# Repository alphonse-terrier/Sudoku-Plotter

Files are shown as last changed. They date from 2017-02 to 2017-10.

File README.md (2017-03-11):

# Sudoku-Plotter

Tous les fichiers permettant la réalisation d' un bras mécanique travaillant en coordonnées polaires, permettant d’écrire un sudoku ou d’en résoudre un et à terme d’écrire tout type d’information.

Au niveau informatique, le bras doit identifier une grille de sudoku tracée sur une feuille, résoudre cette dernière par différentes méthodes de résolution. Ces méthodes doivent permettre éventuellement de créer des grilles de sudoku à compléter. Une fois le sudoku résolu, le stylo présent sur le bras doit pouvoir se déplacer pour écrire la solution de celui-ci (ou écrire un sudoku que l’utilisateur devra lui-même compléter). Le bras doit pouvoir également recopier tout type de document en noir et blanc.

La structure du bras sera réalisée en Makerbeam, tiges en métal se rapprochant dans leur utilisation des meccanos. Le pivotement du bras sera assuré par un moteur pas-à-pas dont le pignon sera en liaison appui-plan avec un roue dentée fixe. Ainsi la mise en mouvement du moteur entrainera sa rotation - et celle de toute la structure - autour de cette roue. Le stylo sera fixé sur une structure qui pourra se déplacer le long de deux tiges en métal. Cette structure sera mise en mouvement par un deuxième moteur pas-à-pas qui entrainera une courroie fixée à ses extrémités à celle-ci. Le stylo pourra être mis en contact avec la feuille grâce à un servomoteur.

La résolution d'un sudoku peut se faire par l'éxécution du fichier main.py dans un interpréteur Python 3.

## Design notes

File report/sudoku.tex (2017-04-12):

\title{Bras mécanique et sudoku}
\author{Laurent Tainturier \& Alphonse TERRIER}
\date{2016-2017}
\documentclass[12pt,a4paper]{report}
\usepackage[utf8]{inputenc}
\usepackage[T1]{fontenc}
\usepackage[french]{babel}
\usepackage{hyperref}
\usepackage{lmodern}
\usepackage{graphicx}
\usepackage{multirow}
\usepackage{listings}
\usepackage{enumitem}
\usepackage{stmaryrd}
\usepackage{animate}
\usepackage{url}
\usepackage{array}
\usepackage{amsmath, amsfonts, amssymb}
%\usepackage{minted}
\usepackage{color}
\usepackage{tabularx}
\usepackage{float}
\usepackage{caption}
\usepackage[backend=biber, autolang=other, sorting=none, style=science]{biblatex}
\usepackage[left=4cm,right=3cm,top=2.5cm,bottom=2.5cm]{geometry}
\usepackage{fancyvrb}
\frenchbsetup{StandardLists=true}
\newtheorem{theo}{Définition}[section]
\definecolor{lightgray}{gray}{.6}
\usepackage[dvipsnames]{xcolor}
\definecolor{yellow}{RGB}{225,220,0}
\hypersetup{pdfborder={0 0 0}}

\newenvironment{changemargin}[2]{\begin{list}{}{%
\setlength{\topsep}{0pt}%
\setlength{\leftmargin}{0pt}%
\setlength{\rightmargin}{0pt}%
\setlength{\listparindent}{\parindent}%
\setlength{\itemindent}{\parindent}%
\setlength{\parsep}{0pt plus 1pt}%
\addtolength{\leftmargin}{#1}%
\addtolength{\rightmargin}{#2}%
}\item }{\end{list}}

\usepackage{placeins}

%\addbibresource{bibli.bib}

\begin{document}
\FloatBarrier

\begin{titlepage}
\begin{changemargin}{-1cm}{0cm}
	\centering
	\vspace{5cm}
	{\scshape\huge Institut Supérieur d'Électronique de Paris \par}
	\vspace{1cm}
	{\scshape\LARGE TIPE\par}
	\vspace{1.5cm}
	{\fontsize{45}{45}\selectfont\bfseries Bras mécanique et sudoku\par}
	\vspace{2cm}
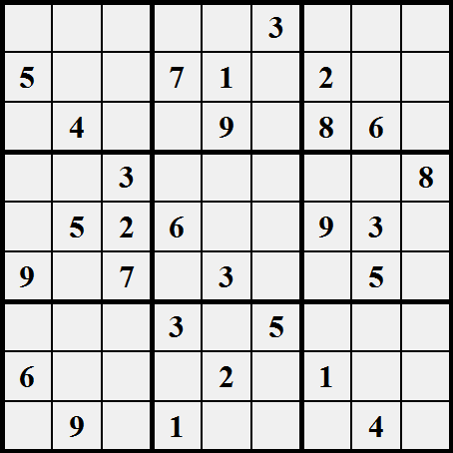
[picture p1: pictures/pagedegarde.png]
	\par\vspace{1.5cm}
	{\LARGE Laurent Tainturier \& Alphonse Terrier\par}
	\vfill
	\large supervisé par\par
	\large \bfseries M. Patrick COUVEZ

	\vfill

	{\large 2016-2017}
\end{changemargin}
\end{titlepage}

\tableofcontents
\addcontentsline{toc}{chapter}{Introduction}
	\chapter*{Introduction}
\footnote{Sauf mention contraire, les images et figures ont été réalisées par nos soins.}
	
	\chapter{Présentation et faits sur le sudoku}
	
	Le sudoku est un jeu sous forme de grille inspiré du carré latin et défini en 1979 par Howard Garns.
	
	Cette grille est carrée et est divisée en $n^2$ régions de $n^2$ cases. Elle possède ainsi $n^2$ colonnes, $n^2$ lignes et $n^4$ cases. Dans la version la plus commune : $n=3$. On appelle section, une ligne, une colonne ou une région

Une grille de sudoku est préremplie, le but du jeu étant de la compléter selon la règle suivante :
\begin{itemize}[label=--]
\item Chaque section doit contenir au moins une fois tous les de $1$ à $n^2$.
\end{itemize} 

Une grille est considérée comme sudoku seulement si sa solution est unique.

Le minimum de cases remplies au préalable pour espérer que la dite solution soit bien unique est de 17, cela a été prouvé par une équipe islandais en 2012.

	\chapter{Mécanique}	
	\section{Choix concernant la structure du bras}
	La premier défi qui s'est imposé à nous a été le choix d'une structure adéquate : solide et pratique. Notre choix s'est alors porté sur les Makerbeam. MakerBeam est un système de construction Open-Source basé sur des profilés ALU en T.
	
	L'écriture se fera en coordonnées polaires et non pas en coordonnées cartésiennes pour les raisons suivantes :
	\begin{itemize}[label=--]
	\item un système en coordonnées cartésiennes aurait été trop encombrant et un moins "portable" (dans un contexte notamment d'optimalité, comme exigé par le programme)
	\item c'est un défi technique de fabriquer un bras de ce type en coordonnées polaires
	\end{itemize}
	
Ainsi, un moteur pas-à-pas assurera la rotation $\theta$ du bras. Ce moteur s'auto-entrainera autour d'une roue dentée de 128 dents comme celle-ci et un roulement permettra la rotation de l'entièreté du bras :

\begin{figure}[!h]
 \center
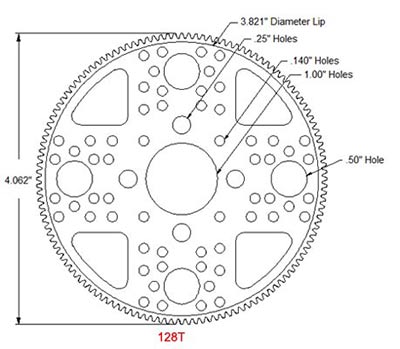
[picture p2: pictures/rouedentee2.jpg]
 
 \caption{Schéma de la roue dentée}
\end{figure}

De même la translation $r$ a été assurée par un deuxième moteur pas-à-pas et un système courroie/poulie. Cette translation s'est faite le long de deux axes de $272$ mm et de $8$ mm de diamètre.

	\section{Étude cinématique du mécanisme}
	La pièce 0 correspondra par la suite au bâti. La base du bras et le bâti seront supposés en liaison encastrement, alors qu'ils sont en réalité en liaison appui-plan, cependant les forces de frottements entre ces deux pièces sont telles quelles sont presque immobiles l'une par rapport à l'autre. La pièce 1 correspond à la structure du bras, reposant sur la roue dentée. La pièce 2 symbolise le chariot et la pièce 3 le stylo.

\begin{figure}[!h]
 \center
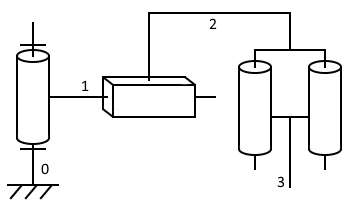
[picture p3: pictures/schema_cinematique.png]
 
 \caption{Schéma cinématique du mécanisme choisi}
\end{figure}

\begin{figure}[!h]
 \center
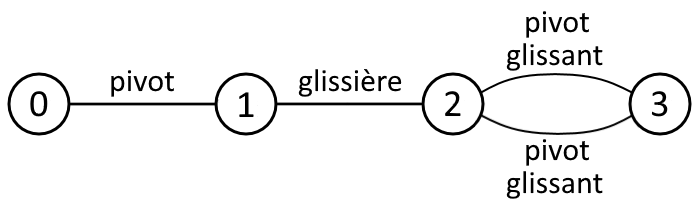
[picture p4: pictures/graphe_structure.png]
 
 \caption{Graphe de structure du mécanisme choisi}
\end{figure}

	Les deux liaisons en parallèle entre 2 et 3 peuvent être remplacés par une liaison équivalent ede torseur $\{ T_c (2/3) \}$ devant vérifier l'équation suivante: : 
	\begin{align*}
\{ T_c (2/3) \}_{B} = \{ T'_c (2/3) \}_{B} = \{ T''_c (2/3) \}_{B}
\end{align*}
On notera les liaisons entre les pièces 2 et 3 $L'_{2/3}$ et $L''_{2/3}$. On a alors:
\begin{align*}
\{ T'_c (2/3) \} =
\begin{array}{c}
	\\ \\ \\ 
\end{array} _{\forall P \in (B,\overrightarrow{z})}
\left\{
\begin{array}{cc}
	0 & 0 \\
	0 & 0 \\
	\gamma'_{2/3} & w'_{2/3} \\
\end{array}
\right\} _{x,y,z)}
\end{align*} 
\begin{align*}
\{ T''_c (2/3) \} = 
\begin{array}{c}
	\\ \\ \\ 
\end{array} _{\forall P \in (C, \overrightarrow{z})}
\left\{
\begin{array}{cc}
	0 & 0 \\
	0 & 0 \\
	\gamma''_{2/3} & w''_{2/3} \\
\end{array}
\right\} _{(x, y, z)}
\end{align*}
\begin{align*}
\mbox{Or } \overrightarrow{V}(B \in 2/3) 
&= \overrightarrow{V}(C \in 2/3)+\overrightarrow{\Omega}(2/3) \wedge \overrightarrow{CB}\\ 
&= w''_{2/3} \overrightarrow{z} + \gamma''_{2/3} \overrightarrow{z} \wedge BC \overrightarrow{x} \\
&= w''_{2/3} \overrightarrow{z} + \gamma''_{2/3}BC \overrightarrow{y}
\end{align*} 
\begin{align*}
\mbox{On a donc }
\{ T''_c (2/3) \} = 
\begin{array}{c}
	\\ \\ \\ 
\end{array} _{B}
\left\{
\begin{array}{cc}
	0 & 0 \\
	0 & \gamma''_{2/3}BC \\
	\gamma''_{2/3} & w''_{2/3} \\
\end{array}
\right\} _{(x, y, z)}
\end{align*}
\begin{align*}
\mbox{Donc }
\{ T_c (2/3) \} = 
\begin{array}{c}
	\\ \\ \\ 
\end{array} _B
\left\{
\begin{array}{cc}
	0 & 0 \\
	0 & 0 \\
	\gamma'_{2/3} & w'_{2/3} \\
\end{array}
\right\} _{x,y,z)} =
\begin{array}{c}
	\\ \\ \\ 
\end{array} _{B}
\left\{
\begin{array}{cc}
	0 & 0 \\
	0 & \gamma''_{2/3}BC \\
	\gamma''_{2/3} & w''_{2/3} \\
\end{array}
\right\} _{(x, y, z)}
\end{align*} 
\begin{align*}
\mbox{D'où le système d'équation : }
\left\{
\begin{array}{l}
0 = 0 \\
0 = 0 \\
\gamma'_{2/3} = \gamma''_{2/3} \\
0 = 0 \\
\gamma''_{2/3} = 0 \\
w'_{2/3} = w''_{2/3} \\
\end{array}
\right. 
\end{align*} 
\begin{align*}
\mbox{On en déduit } 
\{ T_c (2/3) \} = 
\begin{array}{c}
	\\ \\ \\ 
\end{array} _B
\left\{
\begin{array}{cc}
	0 & 0 \\
	0 & 0 \\
	0 & w'_{2/3} \\
\end{array}
\right\} _{x,y,z)}
\end{align*}

La liaison équivalente est donc une liaison glissière d'axe z, ce qui permet des déplacements verticaux du stylo, il peut ainsi être mis en contact avec la feuille.
On a alors le schéma de la figure \ref{Schema_cine_simp}.

\begin{figure}[!h]
 \center
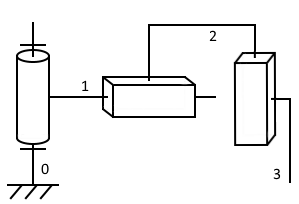
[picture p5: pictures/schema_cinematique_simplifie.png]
 
 \caption{Schéma cinématique équivalent au mécanisme choisi}
 \label{Schema_cine_simp}
\end{figure}

	\section{Difficultés rencontrées et solutions mises en place}
	Nous avons notamment rencontré des difficultés concernant le roulement utilisé. En effet, nous avions au préalable utilisé un roulement à billes comme celui-ci :
	
	\begin{figure}[!h]
 \center
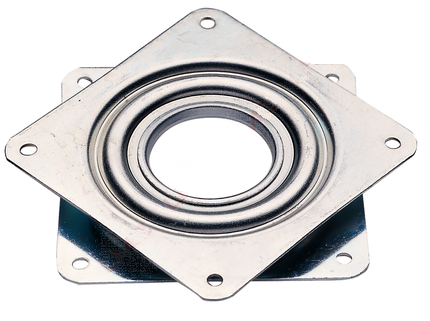
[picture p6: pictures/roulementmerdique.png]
 
 \caption{Roulement défectueux}
\end{figure}

Malheureusement, ce roulement tournait très mal et saccadait. De plus, du jeu était présent. Après quelques heures de recherche, nous avons donc choisi le roulement à billes suivant, qui tourne très bien mais qui tout de même possède lui aussi un peu de jeu :

	\begin{figure}[!h]
 \center
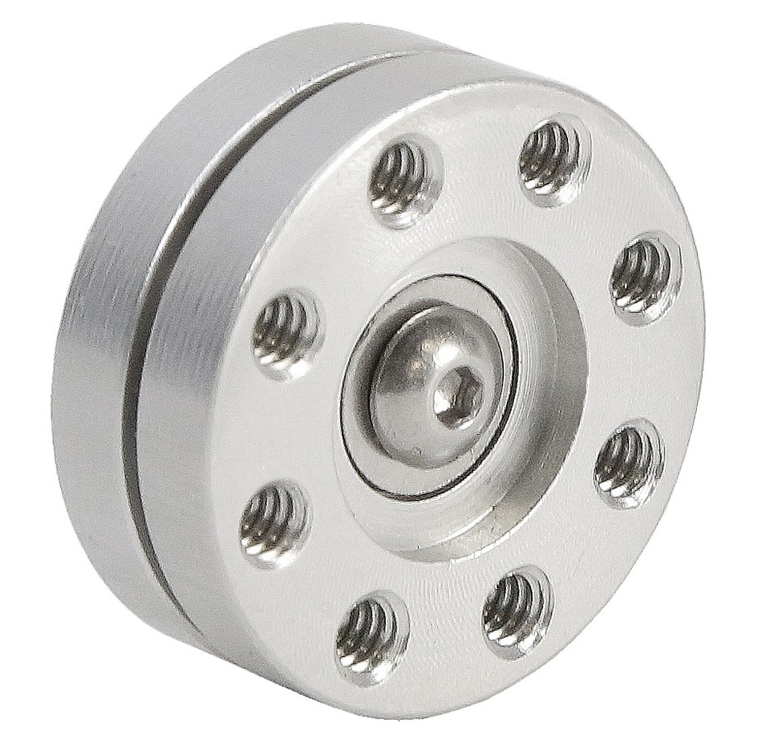
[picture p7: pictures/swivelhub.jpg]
 
 \caption{Roulement finalement choisi}
\end{figure}

	\section{Conception du chariot en 3D}
	Nous avons pris la décision de concevoir certaines pièces de notre projet en 3D, celle-ci nécessitant de la précision. Le logiciel professionnel de modélisation SolidWorks, développé par DassaultSystèmes, a été utilisé pour développer ces pièces.
	
	Les mises en plan des pièces composant le chariot sont disponibles en annexe \ref{chariot} à partir de la page \pageref{chariot}.
	
	La partie principale du chariot devait pouvoir accueillir un servomoteur, permettant l'abaissement et le soulèvement du stylo :
	
	%\begin{figure}[!h]
 %\center
 %\includegraphics[scale=0.15]{../pictures/chariot}
 %\caption{Impression 3D de la pièce principale du chariot}
	%\end{figure}
	
	Ce stylo sera fixé sur la pièce présentée en page \pageref{supportstylo} dont l'impression 3D est montrée ci-dessous :
	
	%\begin{figure}[!h]
 %\center
 %\includegraphics[scale=0.15]{../pictures/supportstylo}
 %\caption{Impression 3D de la pièce supportant le stylo}
	%\end{figure}
	
L'ensemble chariot/support du stylo imprimé en 3D est alors montrée ci-dessous :

	%\begin{figure}[!h]
 %\center
 %\includegraphics[scale=0.15]{../pictures/supportchariot}
 %\caption{Impression 3D du chariot et du support du stylo}
	%\end{figure}

Le chariot permet, de façon modulaire, d'accueillir un support caméra se divisant en deux pièces présentées en page \pageref{chariotcamera} et en page \pageref{supportcamera}.

	\chapter{Électronique}
\section{Moteurs pas-à-pas}
\label{Elec_stepper}
Nous avons utilisé dans ce projet deux moteurs pas-à-pas qui présentaient, par rapport à d'autres types de moteurs, les avantages suivants : 
\begin{itemize}[label=--,itemsep=0pt,font=\bf\Large,labelsep=5mm]
\item une précision bien supérieure à celle de moteurs à courant continu;
\item un couple bien plus important que celui de servomoteurs;
\item mis sous tension, un déplacement fortuit du moteur n'est pas possible.
\end{itemize}
Les moteurs pas-à-pas sont notamment utilisés dans les systèmes nécessitant une grande précision comme les imprimantes 3D dans lesquelles ils sont très largement employés.

\begin{figure}[!h]
 \center
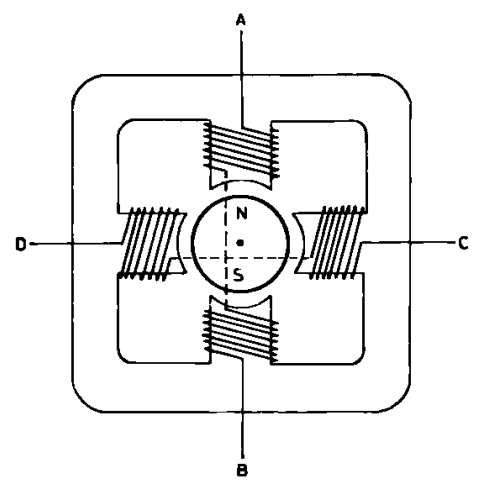
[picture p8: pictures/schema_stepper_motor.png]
 
 \caption{Schéma simplifiée d'un moteur pas-à-pas\protect\footnotemark}
 \label{schema_stepper}
\end{figure}
\footnotetext{\url{http://eskimon.fr/290-arduino-603-petits-pas-le-moteur-pas-pas}}

\paragraph{} Les moteurs que nous avons utilisés sont constitués de deux bobines, repliées tout autour de la partie centrale du moteur, permettant des petits déplacements de la partie mobile. Celles-ci sont divisées en deux sur la figure \ref{schema_stepper}. La bobine 1 a pour extrémités A et B; la bobine 2 C et D. Ces bobines, lorsqu'elles sont parcourues par un courant i, génèrent un champ magnétique. Ce champ magnétique a pour conséquence d'entrainer la rotation de la partie mobile du moteur : le rotor, représenté par le cercle centrale N/S. Celui-ci est composé d'un aimant qui a tendance a s'aligner sur le champ magnétique créé par les bobines. 
Les bobines sont enroulées autour d'un fer doux, généralement de la ferrite afin de mieux conduire le lignes de champs.

\paragraph{} On distingue deux types de fonctionnement pour ces moteurs bipolaires, un fonctionnement à demi-pas et un fonctionnement à pas complet. Nous avons retenu ce dernier système car il permettait d'obtenir une vitesse et un couple constants lors de la rotation des moteurs. 
Comme le montre la figure \ref{Motor_min}, à chaque séquence, une seule bobine suffirait à mettre en mouvement le moteur, cependant nous avons choisi d'alimenter tout de même l'autre afin d'obtenir un couple maximal (cf figure \ref{Motor_max}). 

\begin{center}
\renewcommand{\arraystretch}{1.25}
\begin{tabularx}{0.49\linewidth}{|c|*{5}{>{\centering \arraybackslash}X|}}\hline
\multirow{2}*{Séquence} & \multicolumn{2}{c|}{Bobine 1}  & \multicolumn{2}{c|}{Bobine 2} \\
\cline{2-5} & \centering A & \centering B & \centering C & D \\ \hline  
1 & 1 & 0 & - & - \\ \hline
2 & - & - & 0 & 1 \\ \hline
3 & 0 & 1 & - & - \\ \hline
4 & - & - & 1 & 0 \\ \hline
5 & 1 & 0 & - & - \\ \hline
\end{tabularx}
\captionof{table}{Séquences d'alimentation des bobines avec un couple minimal}
\end{center}

\begin{center}
\renewcommand{\arraystretch}{1.25}
\begin{tabularx}{0.49\linewidth}{|c|*{5}{>{\centering \arraybackslash}X|}}\hline
\multirow{2}*{Séquence} & \multicolumn{2}{c|}{Bobine 1}  & \multicolumn{2}{c|}{Bobine 2} \\
\cline{2-5} & \centering A & \centering B & \centering C & D \\ \hline  
1 & 1 & 0 & 0 & 1 \\ \hline
2 & 0 & 1 & 0 & 1 \\ \hline
3 & 0 & 1 & 1 & 0 \\ \hline
4 & 1 & 0 & 1 & 0 \\ \hline
5 & 1 & 0 & 0 & 1 \\ \hline
\end{tabularx}
\captionof{table}{Séquences d'alimentation des bobines avec un couple maximal}
\end{center}

\begin{center}
\begin{figure}[!h]
 \center
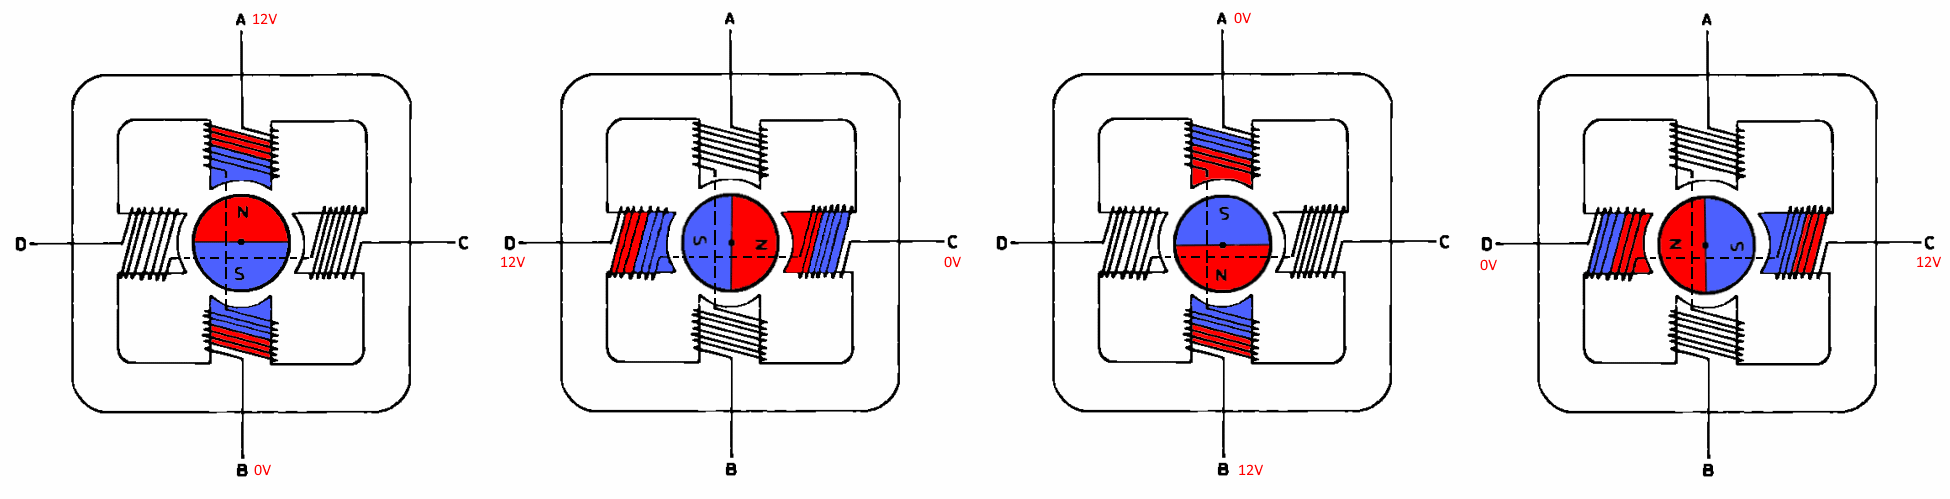
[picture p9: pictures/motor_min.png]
 
 \caption{Fonctionnement à pas complet avec un couple minimal\protect\footnotemark}
 \label{Motor_min}
\end{figure}
\footnotetext{Une animation du pas complet avec couple minimal est disponible sur \url{www.github.com/alphter/Sudoku-Plotter/blob/master/pictures/motor_min1.gif}}

\begin{figure}[!h]
 \center
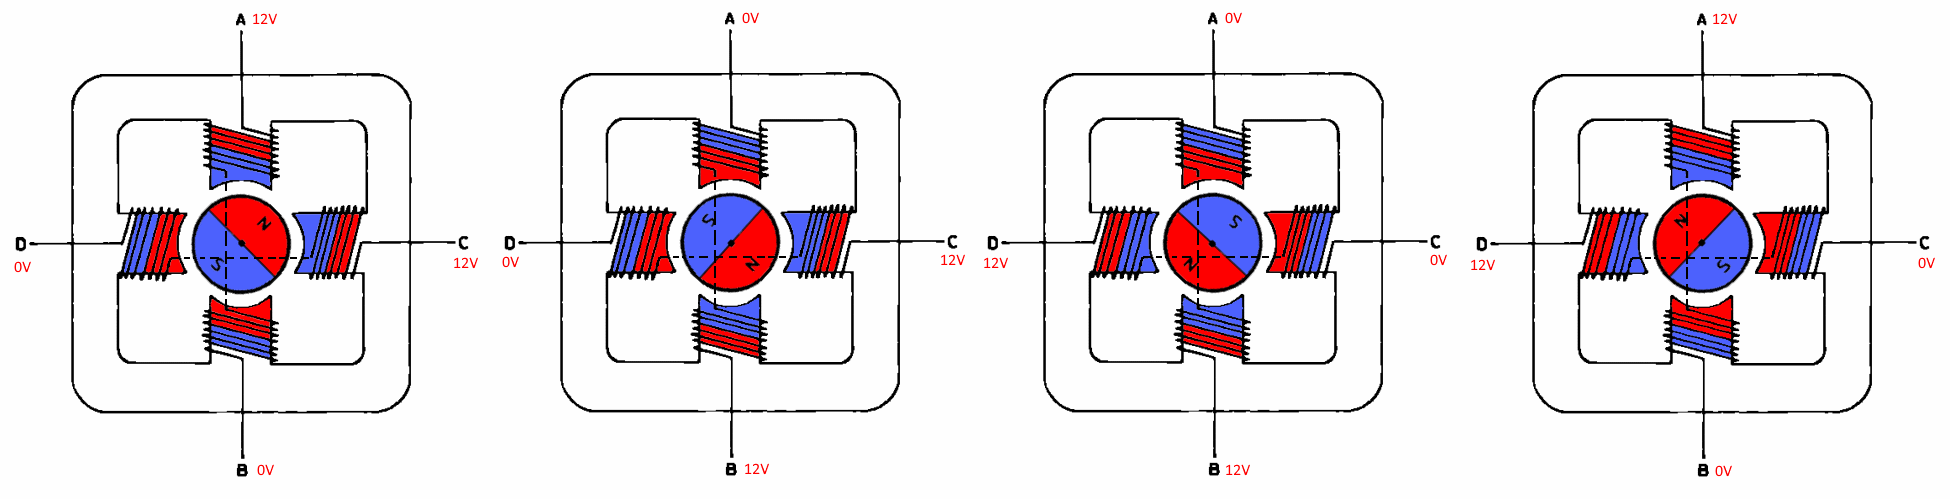
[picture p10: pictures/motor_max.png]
 
 \caption{Fonctionnement à pas complet avec un couple maximal\protect\footnotemark}
 \label{Motor_max}
\end{figure}
\end{center}
\footnotetext{Une animation du pas complet avec couple maximal est disponible sur \url{www.github.com/alphter/Sudoku-Plotter/blob/master/pictures/motor_max1.gif}}

Une autre différence entre l'alimentation d'une ou deux bobines réside dans la position de l'axe des deux moteurs, la position de celui-ci est décalé d'un demi-pas. Le fonctionnement en demi-pas se base ainsi sur la combinaison de ces deux méthodes, ce qui entraîne un couple variable mais permet des déplacements plus précis.

\section{Drivers L293D}
Pour piloter les moteurs, nous utilisons des drivers L293D. Ces drivers présentent les avantages suivants :
\begin{itemize}[label=--,itemsep=0pt,font=\bf\Large,labelsep=5mm]
\item ils permettent l'utilisation d'une source de tension externe, la \emph{Raspberry} ne pouvant fournir que du 5V;
\item ils intègrent deux ponts en H permettant d'inverser le courant circulant dans les bobines;
\item ils permettent d'éviter la création de courants induits dans la \emph{Raspberry}, du faits des bobines, pouvant potentiellement l'endommager ou la détruire.
\end{itemize}

\begin{figure}[!h]
 \center
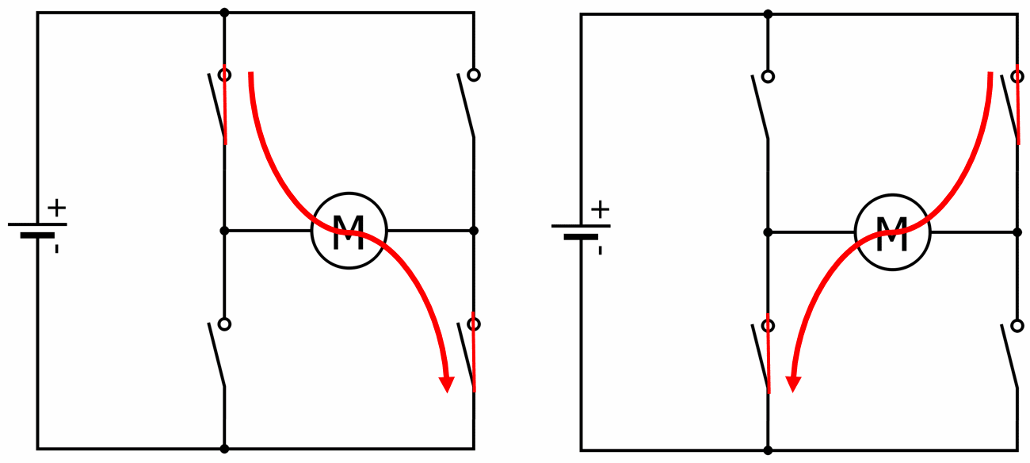
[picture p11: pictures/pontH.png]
 
 \caption{Utilité du pont en H, réalisé avec \emph{QElectroTech}}
 \label{pontH}
\end{figure}

Les ponts en H permettent l'alimentation d'une bobine dans les deux sens, ils permettent également de freiner le moteur en le court-circuitant. Celui-ci est constitué de quatre interrupteurs, conformément à la figure \ref{pontH}. Le moteur M représente une bobine. Les ponts en H sont utilisés dans quasiment tous les drivers des moteurs, que ce soit des moteurs continus ou des pas-à-pas. Les interrupteurs sont alors remplacés par des transistors, ce qui permet de les commander par une autre source d'alimentation (par exemple du 5V). Pour éviter la création de courants induits dans les bobines, on place généralement des diodes en parallèle des transistors (ou des interrupteurs). 

\begin{figure}[!h]
 \center
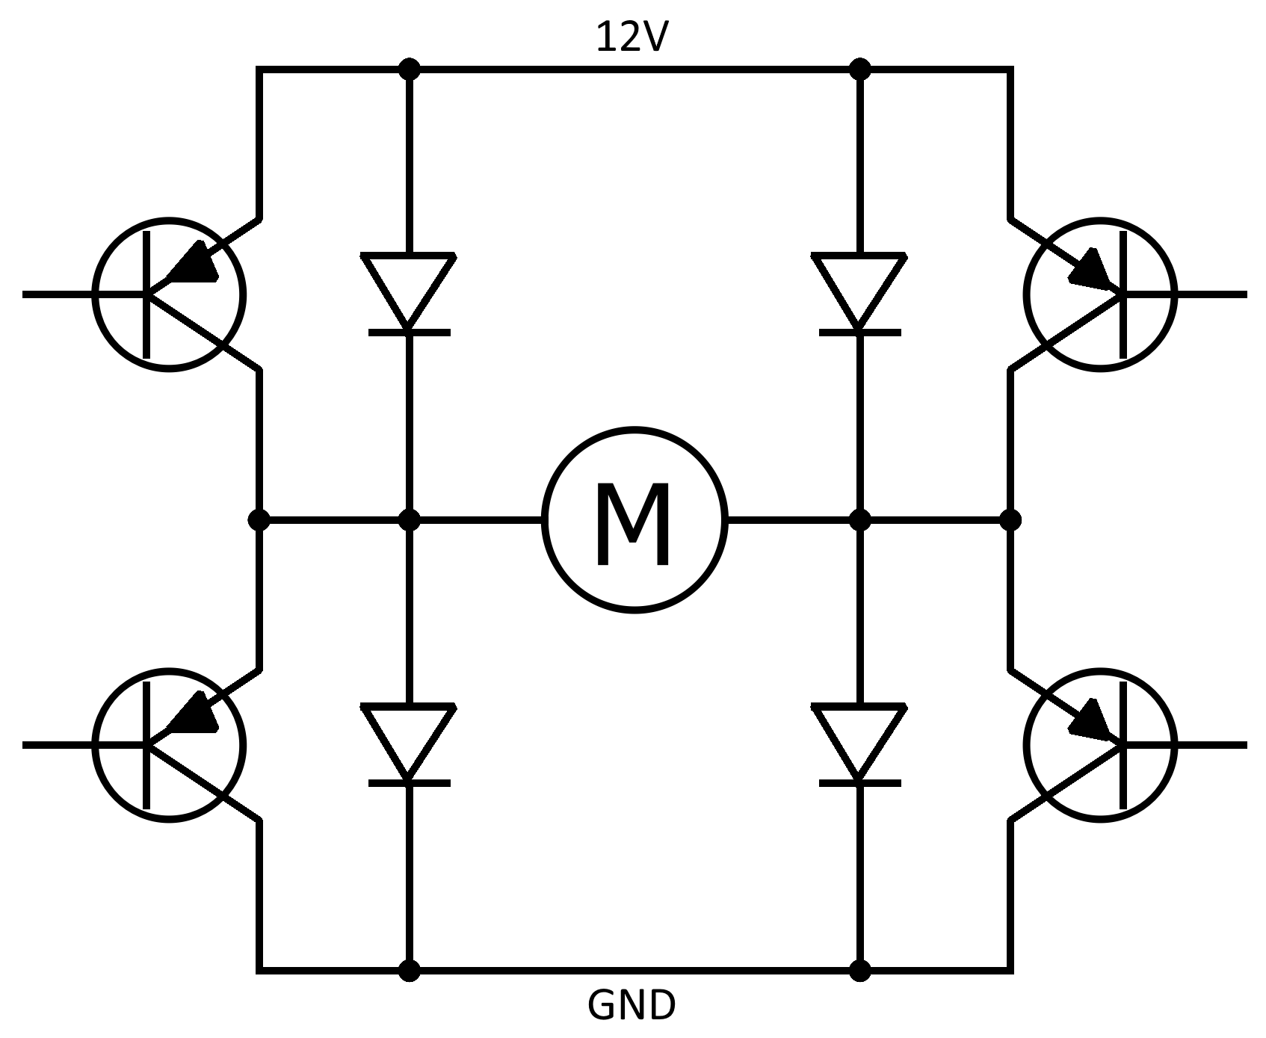
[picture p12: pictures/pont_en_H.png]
 
 \caption{Pont en H intégré dans les drivers, réalisé avec \emph{QElectroTech}}
 \label{pontH}
\end{figure}

Le driver L293D présente l'avantage d'intégrer deux pont en H ainsi que les diodes en parallèle ce qui permet des branchements aisés, sans besoin d'ajout d'autres composants. Comme nos moteurs intègrent deux bobines chacun, nous avons eu besoin de deux L293D, un par moteur.

\section{Schéma électrique}
Le schéma ci-joint représente les principales connections au sein de notre montage, même s'il ne présente ni l'écran LCD, ni le détail de l'alimentation de la \emph{Raspberry Pi} (notamment du convertisseur de tension).

Les moteurs deux bobines de chaque moteur sont reliées aux deux drivers l293D . Ceux-ci sont pilotés par quatre sorties GPIO qui envoient des impulsions au driver qui alimente les bobines en 12V à tour de rôle, ce qui permet à la fois de contrôler le sens et la vitesse de de rotation des moteurs, en choisissant à quelle fréquence envoyer les impulsions. La figure \ref{schema_elec} souligne la présence de deux alimentations différentes, à la fois l'alimentation 5V pour la \emph{Raspberry Pi} et l'alimentation 9V(ou 12V) pour alimenter les moteurs.
\begin{figure}[!h]
 \center
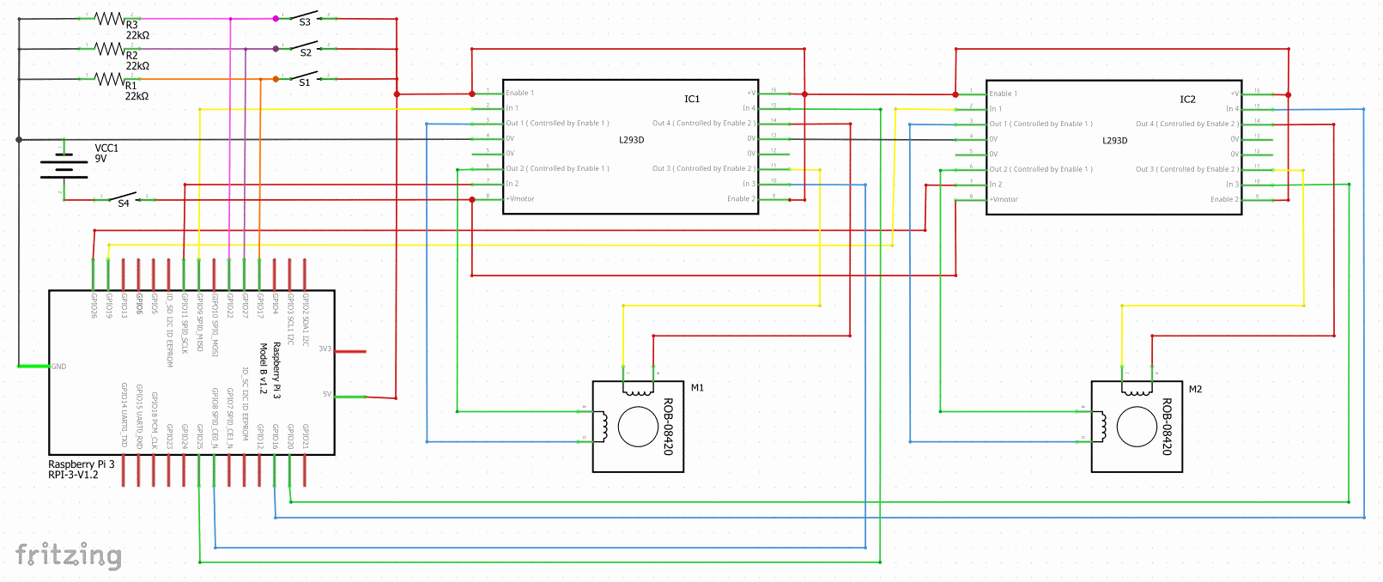
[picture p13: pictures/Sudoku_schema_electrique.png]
 
 \caption{Schéma électrique réalisé avec \emph{Fritzing}}
 \label{schema_elec}
\end{figure}

\newpage
\section{Premiers montages}
Nous avons réalisés nos premiers montages avec une breadboard facilitant les tests. Une simulation du schéma a également été réalisée sous \emph{Fritzing} :

\begin{figure}[!h]
 \center
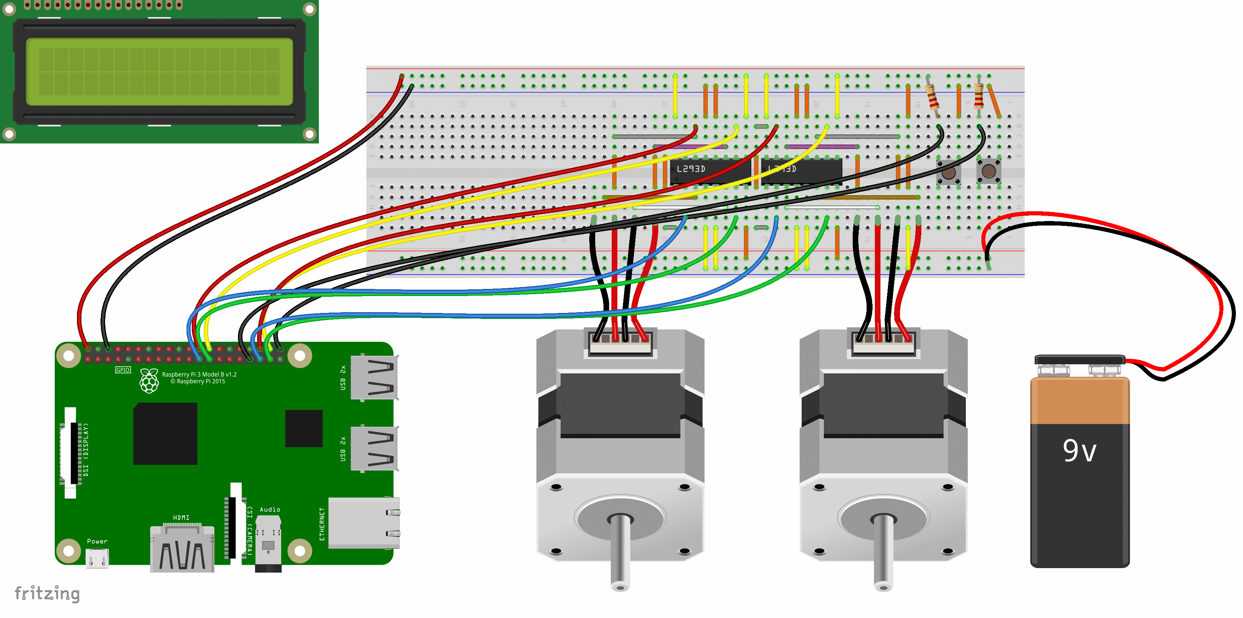
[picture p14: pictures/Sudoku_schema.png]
 
 \caption{Premier montage réalisé avec \emph{Fritzing}}
\end{figure}

\section{Circuit imprimé}
Pour rendre notre bras mécanique plus compact et ainsi rentrer dans le cadre de l'optimalité, nous avons souhaité remplacer la breadboard par une solution bien plus compacte, à savoir un circuit imprimé. Celui-ci sera enficher directement sur les ports GPIO de la Raspberry Pi. Nous avons de nouveau utilisé pour le réaliser le logiciel \emph{Fritzing}, permettant la réalisation du circuit sur deux couches (symbolisées par les couleurs orange et jaune), permettant un cablage plus facile, car autorisant les croisements. Nous avons utilisé \emph{Fritzing} car il été assez facile de faire faire fabriquer le circuit imprimé pour une dizaine d'euros. Nous avions hésité à réaliser entièrement ce circuit par nous même, mais du fait de la présence des deux couches, cela se serait révélé très difficile et aurait sans doute coûté plus cher.

\begin{figure}[!h]
 \center
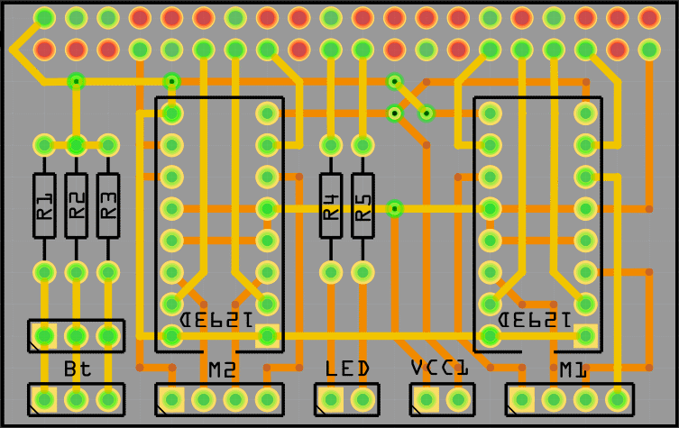
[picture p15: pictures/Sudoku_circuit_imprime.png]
 
 \caption{Circuit imprimé réalisé avec \emph{Fritzing}}
\end{figure}

\section{Écran LCD}
Pour rendre le bras mécanique plus autonome, nous avons intégré un écran LCD permettant à l'utilisateur de se repérer dans l'évolution des différents scripts sans disposer nécessairement d'un ordinateur ou d'un écran à proximité, ce qui permettait une utilisation facilitée de celui-ci. L'écran utilisé est un écran LCD 2x16, disposant d'un potentiomètre intégré permettant de régler la luminosité de l'écran. Il dispose de quatre sorties, à savoir une sortie 5V, la masse et deux sorties pour envoyer les informations.

\begin{figure}[!h]
 \center
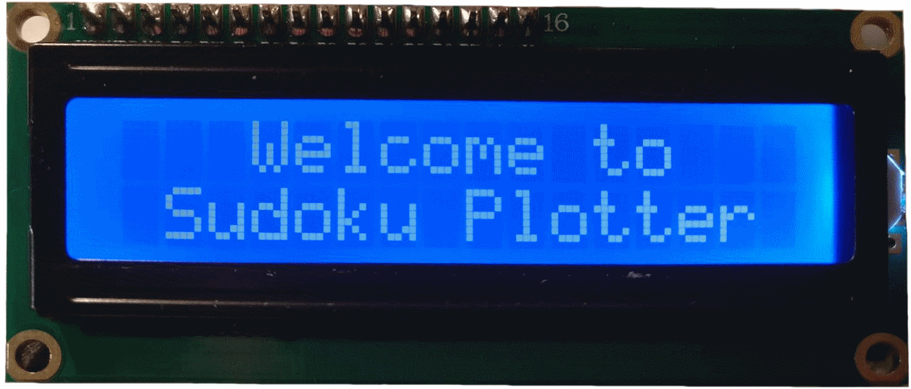
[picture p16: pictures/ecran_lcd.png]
 
 \caption{\'{E}cran LCD affichant le message de bienvenue}
\end{figure}

	\chapter{Informatique}
\section{Présentation globale}
	Tous les algorithmes développés dans le cadre de ce projet sont disponibles en annexe. Ils ont été, pour la plupart, développés sous Python 3, les autres sous Python 2 car certaines bibliothèques dont nous avions besoin, notamment pour la reconnaissance, n'était disponible que sous Python 2. 
	
	Nous avons développé une programmation modulaire, permettant de travailler simultanément sur le projet, sans pour autant poser de problème de logistique. Ainsi nous avons dissocié tous les scripts ; que ce soit la reconnaissance, la résolution, l'affichage, la gestion de la caméra ou des moteurs, etc. Pour cela, nous avons développé une relation qualifiable de maître-esclave entre nos scripts. Chacun des scripts dépend d'un fichier principal, appelé \emph{main}, qui récupère les informations des autres scripts et donne les ordres adéquats à ceux-ci, selon la situation. Ainsi, les scripts ne sont pas reliés les uns aux autres mais seulement à ce script principal, ce qui permet d'ajouter ou d'enlever très facilement tel ou tel script, sans pour autant altérer le fonctionnement de l'ensemble, permettant ainsi de tester chacun des scripts très facilement.
	
\section{Reconnaissance du sudoku}
	Le script de reconnaissance du sudoku a été réalisé sous Python 2 avec le module de traitements d'image OpenCV. Il a été réalisé pour :
	\begin{itemize}[label=--]
	\item Reconnaître les chiffres dans une grille du sudoku
	\item Déterminer la position spatiale de la grille
	\end{itemize}
	On photographie la grille avec une caméra Raspberry Pi (V2) comme celle-ci :
\begin{figure}[!h]
 \center
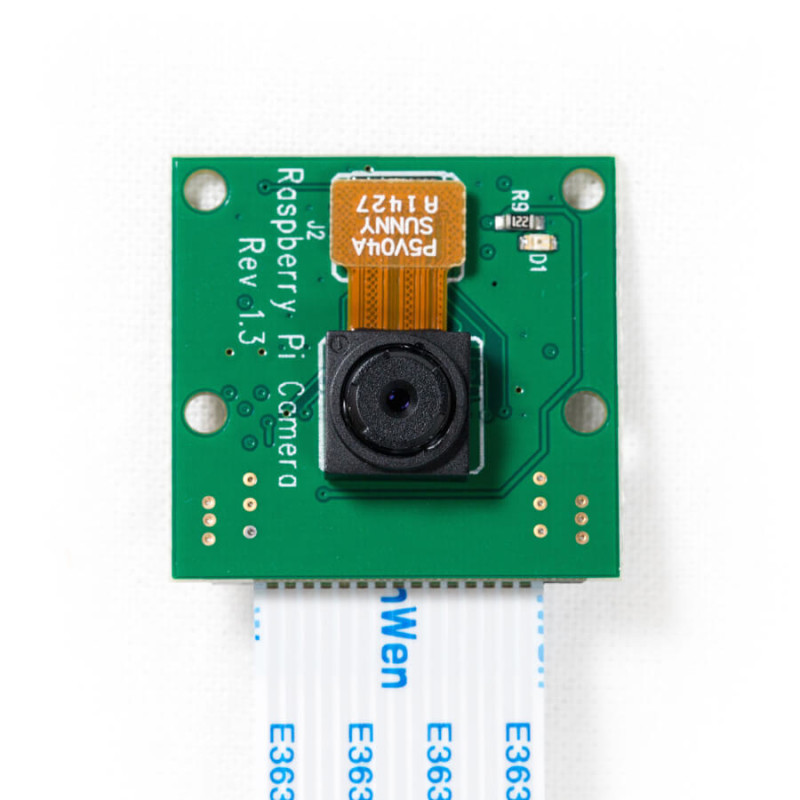
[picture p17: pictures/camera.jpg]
 
 \caption{Caméra Raspberry Pi V2}
\end{figure}

Voici la grille de sudoku qui nous servira d'exemple pour montrer toutes les actions du script :
\begin{figure}[!h]
 \center
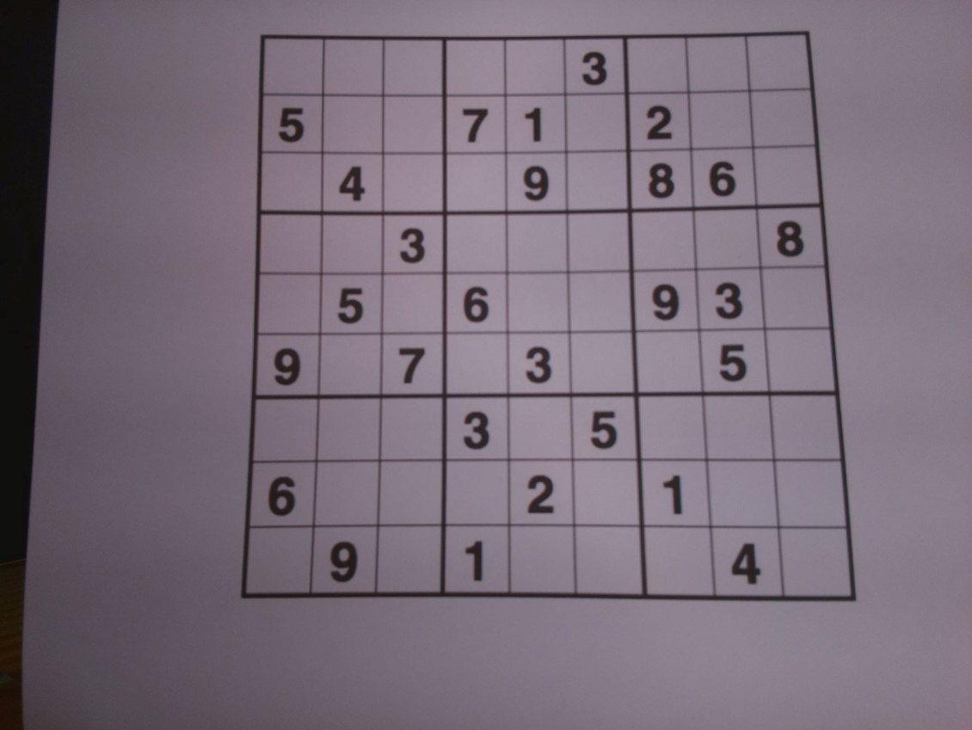
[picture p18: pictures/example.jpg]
 
 \caption{Exemple de grille de sudoku}
\end{figure}
\newpage
On applique sur cette photographie un filtre de type seuil (en anglais "threshold") qui va ensuite nous permettre de détecter les contours de la grille :

\begin{figure}[!h]
 \center
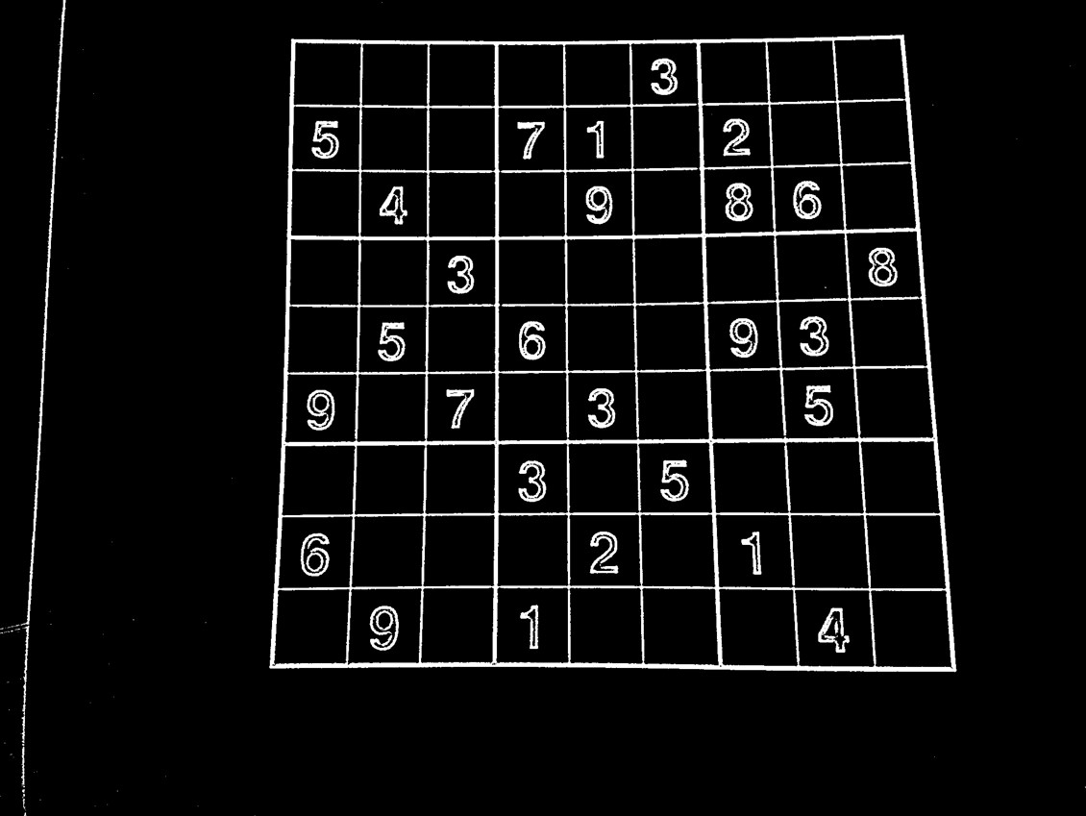
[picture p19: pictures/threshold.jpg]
 
 \caption{Exemple de grille "seuillée"}
 \end{figure}
 
Par cette transformation, on peut ensuite déterminer des équations de droites des contours extérieurs de la grille. Les coordonnées des intersections des droites seront celle des coins de la grille. \smallbreak On découpe alors la grille de la photographie initiale en supprimant les éventuels effets de perspective. 
 
\begin{figure}[!h]
 \center
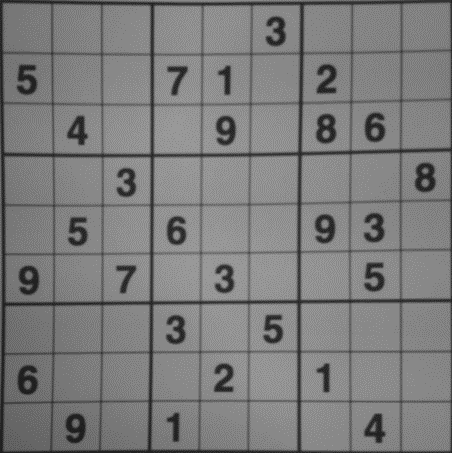
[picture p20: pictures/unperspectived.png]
 
 \caption{Exemple de grille découpée sans perspective}
\end{figure}

On découpe chaque petite case de la grille comme ci-dessous :

\begin{figure}[!h]
 \center
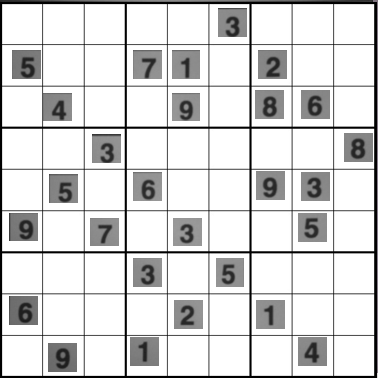
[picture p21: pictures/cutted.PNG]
 
 \caption{Exemple de grille où chaque chiffre a été découpé}
\end{figure}

On utilise ensuite un module de reconnaissance de digits pour détecter les chiffres et on obtient la grille suivante, prête à être résolue :

\begin{figure}[!h]
 \center
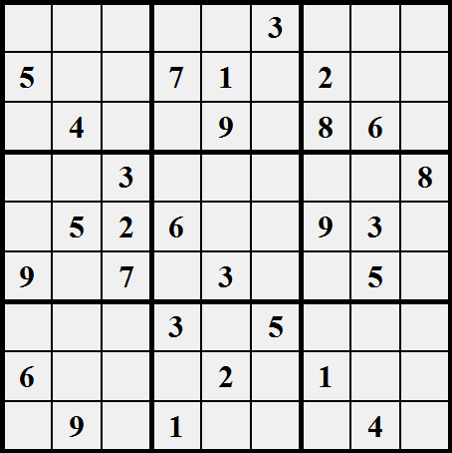
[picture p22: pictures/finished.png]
 
 \caption{Exemple de grille prête à être résolue}
\end{figure}

\newpage
\section{Résolution du sudoku}
\label{Resolution}
Pour résoudre une grille de sudoku, un joueur utilise différentes méthodes de résolution, qui sont purement algorithmiques. Il utilise en grande majorité deux méthodes qui peuvent permettre de résoudre une grande partie des grilles disponibles sur le marché. On appelle ces deux méthodes \emph{inclusion} et \emph{exclusion}. Cependant les grilles de niveau supérieur font appel à des méthodes plus subtiles et souvent plus difficiles à appliquer en pratique qui se basent généralement sur des \emph{paires} ou des \emph{triplets}. Les grilles les plus difficiles peuvent imposer au joueur de faire un choix entre plusieurs possibilités pour espérer mener à son terme la résolution. C'est sur ce constat que ce base la méthode dite de \emph{backtracking} (ou \emph{retour sur trace}), qui permet de résoudre toute grille de sudoku, même si celle-ci n'est pas valide et possède plusieurs solutions. Bien sûr cette liste n'est pas exhaustive et il existe d'autres méthodes de résolution, même si ces méthodes ne sont pas forcément très employées et faciles d'emploi.

\paragraph{Inclusion: un seul candidat pour une case}
On dénombre pour chaque case vierge les chiffres pouvant être positionnés dans celle-ci. S'il n'y a qu'une seule possibilité alors elle est solution et est donc placée dans la case.
\begin{figure}[!h]
 \center
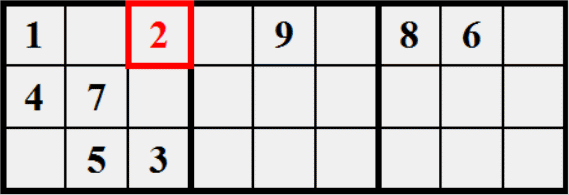
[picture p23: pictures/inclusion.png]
 
 \caption{Méthode d'inclusion pour une région}
\end{figure}

\paragraph{Exclusion: candidat unique pour une section}
Si pour un chiffre donné, on ne peut le placer dans une section que dans une seule case possible, alors ce chiffre est placé dans cette case
\begin{figure}[!h]
 \center
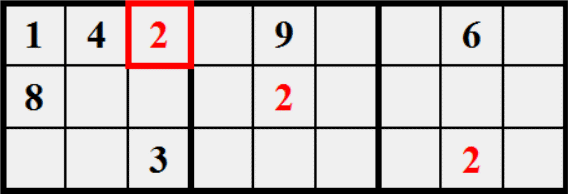
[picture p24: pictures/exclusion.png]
 
 \caption{Méthode d'exclusion pour une région}
\end{figure}

\paragraph{Paires} Si dans une section donnée, deux cases ne contiennent que deux \emph{candidats identiques}, alors ils ne peuvent être placés que dans ces deux cases, ce qui permet de les éliminer des autres possibilité pour la section
\begin{figure}[!h]
 \center
 
 \caption{Méthode des paires pour une ligne}
\end{figure}

La méthode des triplets est une généralisation de cette méthode à trois cases et non seulement deux.

\paragraph{Jumeaux} Si dans une section, un chiffre ne peut être placé que sur une ligne (resp. colonne), alors ce chiffre peut être supprimé des possibilités pour le reste de la ligne (resp.colonne). Cette méthode ne permet pas toujours de placer immédiatement celui-ci, mais permet de réduire les possibilités pour placer les autres.
\begin{figure}[!h]
 \center
 
 \caption{Méthode des jumeaux pour une ligne}
\end{figure}

\paragraph{Backtracking} Cette méthode\footnote{Une animation du \emph{backtracking} est disponible sur : \url{www.github.com/alphter/Sudoku-Plotter/blob/master/pictures/backtracking.gif}} consiste tout d'abord à lister pour chacune des cases vierges les chiffres qui pourraient correspondre. On part d'une case vierge quelconque qu'on remplit par un des chiffres pouvant théoriquement convenir, puis on liste les nouvelles possibilités des autres cases en fonction du chiffre précédemment ajouté puis on passe à la case suivante. S'il n'y a plus aucune possibilité, on revient sur nos pas et on change le chiffre qu'on venait d'ajouter en une autre possibilité. Si tout les chiffres possibles ont été testé, on revient de nouveau sur nos pas autant de fois que nécessaire, jusqu'à avoir compéter la totalité de la grille. 

\begin{center}
	\animategraphics[width=0.55\linewidth]{12}{../gif/backtracking/backtracking-}{0}{283}
\end{center}

\paragraph{} Partant de ce constat, nous avons tout d'abord implémenté la méthode de \emph{backtracking}, ainsi, il nous était possible de résoudre toutes les grilles possibles. \`{A} l'origine, notre algorithme parcourait la grille dans un ordre prédéfini, à savoir de haut en bas et de gauche à droite. Cependant, il pouvait arriver que pour certaines grilles, ce système n'était pas tout à fait optimale. C'est pourquoi, nous l'avons changé de sorte que l'algorithme commence par les cases présentant le moins de possibilités, permettant dans le cas général de diminuer le temps de résolution. Cependant, dans le pire des cas, cette solution ne présentait aucune différence en terme de temps de calculs. 

\paragraph{Temps de calculs} Au niveau informatique, ces méthodes ne se valent pas dans la mesure où elles sont plus ou moins fiables, efficaces et rapides. L'\emph{inclusion} et l'\emph{exclusion} sont comparables : elles sont rapides et efficaces mais ne permettent pas la résolution complète dans un certain nombre de cas. L'utilisation du \emph{backtracking} se révèle alors efficace en complément des deux précédentes, puisque cette méthode permet toujours de conclure. Les temps de calculs sont comparables pour toutes ces méthodes et sont de l'ordre du centième de secondes\footnote{Les résultats peuvent varier d'un machine à l'autre comme nous avons pu le constater, il est donc surtout intéressant de noter les différences d'ordres de grandeurs entre les différents résultats.}. La résolution peut parfois prendre plus d'une seconde mais cette situation ne s'est présentée que très rarement. Cependant, il peut arriver que pour des grilles très particulières, conçues pour tester la rapidité du \emph{backtracking}, la résolution du sudoku prenne bien plus de temps, jusqu'à 30 secondes. En utilisant les trois méthodes de manière couplée, le temps de calculs diminue pour arriver à seulement 20 secondes. Une utilisation couplée des méthodes est bien plus efficace car permet d'éliminer immédiatement toutes les possibilités évidentes, indétectables en \emph{backtracking}, pour ensuite l'utiliser éventuellement si la grille n'est pas résolue.

\newpage
\section{Interface graphique}
Pour rendre la résolution plus simple d'utilisation, nous avons décidé d'ajouter une interface graphique. Le cahier des charges qu'elle devait vérifier était assez stricte. Elle devait pouvoir afficher, avant toute chose, une grille de sudoku qui devait dès lors être facilement modifiable. Pour cela, nous avons donc créé différents menus ; l'un permettant donc l'édition de la grille, un autre permettant de choisir la méthode de résolution, ainsi qu'un menu de résolution. 

\begin{figure}[!h]
 \center
 
 \caption{Interface graphique du Sudoku}
 \label{Menu_edition}
\end{figure}

\paragraph{Édition} Lors de l'édition de la grille, un carré rouge apparait, déplaçable avec les flèches directionnelles, il suffit alors pour modifier la case de rentrer un chiffre de 0 à 9, 0 correspondant à une case vierge. Il est également possible de sauvegarder une grille ou encore de récupérer une grille déjà enregistrée.

\begin{figure}[!h]
 \center
 
 \caption{Menu \emph{Édition} de l'interface graphique}
 \label{Menu_edition}
\end{figure}

\paragraph{Résolution}Ce menu permet de lancer la résolution, et permet également de choisir entre une résolution rapide ou une résolution pas-à-pas permettant à l'utilisateur d'observer le fonctionnement de ces algorithmes.

\begin{figure}[!h]
 \center
 
 \caption{Menu \emph{Résolution} de l'interface graphique}
\end{figure}

\paragraph{Méthode}Le choix de la méthode se fait avec le menu \emph{Méthode}, qui permet de choisir la méthode de résolution parmi l'\emph{inclusion}, l'\emph{exclusion} et le \emph{backtracking} ou de choisir une méthode dite \emph{globale}, s'appuyant sur tous ces algorithmes, permettant ainsi d'être la plus rapide possible.

\section{Contrôle des moteurs et écriture}
\subsection*{Moteurs pas-à-pas}
Il nous apparaissait nécessaire de développer une programmation permettant l'exécution simultanée de plusieurs instructions, notamment pour les moteurs. En effet, les moteurs doivent absolument fonctionner de manière synchrone afin d'obtenir des déplacements les plus précis possibles. C'est pour cela que nous nous sommes basés sur ce qui pourrait être qualifiée de "programmation parallèle" qui permet l'exécution de plusieurs processus simultanément. Cela est rendu possible en Python par l'utilisation de la bibliothèque \emph{threading} depuis laquelle nous utilisons \emph{Thread} (signifiant \emph{processus} en français). 
Pour piloter les moteurs, il suffit d'envoyer des impulsions dans les bobines pour faire tourner les moteurs dans le bon sens. La fréquence d'envoi de ces impulsions conditionne la vitesse des moteurs. Les impulsions doivent être envoyés au maximum toute les 10 ms, ce qui constitue la vitesse maximum des moteurs. Ces impulsions sont envoyés au deux moteurs de manière cycliques, un cycle étant constitué de quatre séquences\footnote{cf section \ref{Elec_stepper} à la page \pageref{Elec_stepper}}. Le script d'écriture des digits transmet à celui des moteurs une liste des coordonnées des points à parcourir. Ces coordonnées sont ensuite converties en déplacements élémentaires pour les deux moteurs, ce qui se traduit alors en impulsions et permet les déplacements des moteurs.

\subsection*{Coordonnées polaires}
Par soucis de compacité et ainsi s'inscrire dans l'optimalité du programme, nous avons décidé de développer une structure se basant sur les coordonnées polaires, permettant des dimensions maximum de 40 par 10 cm. L'utilisation de telles coordonnées nécessitait une plus grande précision et relevait donc d'un plus grand défi technique. Les coordonnées polaires ne sont de plus, que très peu utilisés pour ce type de système, ce qui nous à incité à développer une structure se basant sur ces coordonnées.

\begin{figure}[!h]
 \center
 
 \caption{Changement de repères réalisé avec \emph{Geogebra}}
 \label{polaire}
\end{figure}

Sur la figure \ref{polaire}, le point $O_1$ correspond au centre de la roue dentée. Le point $A$ correspond à la position du bras et le point $B$ correspond à la position que l'on souhaite atteindre. On peut noter que le bras doit pivoter d'un angle $\theta = 0.74$ rad et doit se déplacer d'une distance algébrique r pour atteindre ce point $B$. Ces deux données sont transmises aux moteurs qui vont se déplacer d'un nombre de pas équivalent pour l'un à $\theta$ et pour l'autre à $r$. On comprend alors qu'il faut suffisamment de points pour éviter de tracer des lignes courbes, en effet si $A$ et $B$ se situent à la même distance du centre $O_1$, le stylo tracera un arc de cercle
Pour avoir accès à $\theta$ et $r$, il faut convertir les coordonnées des point $A$ et $B$ en coordonnées polaires de centre $O_1$. On notera $x_A$ et $y_A$ les coordonnées cartésiennes du point $A$ et $r_A$ et $\theta_A$ ses coordonnées polaires de centre $O_1$. Les coordonnées du point $O_1$ seront eux indicées par 0. On a alors :
\begin{align*}
\left\{
\begin{array}{c}
	x_A = r_A \cdot \cos \theta + x_0 \\ \\
	y_A = r_A \cdot \cos \theta + y_0  \\
\end{array}
\right.
\mbox{ et }
\left\{
\begin{array}{c}
	r_A = \sqrt{(x_A - x_0)^2 + (y_A - y_0)^2} \\ \\
	\theta_A = \frac{y_A - y_0}{|y_A - y_0|} \cdot \arccos \left( \dfrac{y_A - y_0}{r_A} \right) \\
\end{array}
\right.
\end{align*}
Comme $r_A = 0 \iff A = O_1$ et que $A$ est un point de la feuille alors que $O_1$ ne l'est pas, $r_A$ ne peut être nul\footnote{De plus, du fait du mécanisme, le point $O_1$ ne peut pas être atteint par le stylo}. On en déduit que $\theta_A$ est bien définie quelque soit $A$. En notant $nb_{step1}$ (resp. $nb_{step2}$) le nombre de déplacements élémentaires du moteur 1 (resp. du moteur 2), on obtient :
\begin{align*}
\left\{
\begin{array}{c}
	r = r_B - r_A \\ \\
	\theta = \theta_A - \theta_B  \\
\end{array}
\right.
\mbox{ et }
\left\{
\begin{array}{c}
	nb_{step1} = E(\frac{r}{r_{step}} + \frac{1}{2})\\ \\
	nb_{step2} = E(\frac{\theta}{\theta_{step}} + \frac{1}{2})\\
\end{array}
\right. 
\end{align*}
Les entiers relatifs $nb_{step1}$ et $nb_{step2}$ sont les deux informations véritablement importantes pour les moteurs et qui correspondent aux nombre de séquences de leurs déplacements.

\subsection*{Écriture des digits}
Nous souhaitions dès le début pouvoir écrire des grilles de différentes tailles, et non des grilles de tailles fixes. C'est pourquoi nous avons basé le script d'écriture sur du point par point, permettant de choisir la précision théorique des chiffres tracés. Cependant les moteurs pas-à-pas ne pouvant se déplacer que d'un pas fixé de 1.8\degre, une trop grande précision ne pourrait entraînerait que des déplacements nuls des moteurs, c'est pourquoi cette manière de programmation permet un compromis entre précision théorique et précision pratique.

\begin{figure}[!h]
 \center
 
 \caption{Chiffres d'une précision théorique assez faible}
\end{figure}

Le script permettant de tracer les chiffres prend deux paramètres, à savoir la hauteur des chiffres et la précision attendue. Lors des tests du bras mécanique, ces deux paramètres se sont révélés déterminants pour obtenir le meilleur résultat possible. Les chiffres en tant que tel sont constitués de lignes et d'arc de cercle permettant d'obtenir un résultats assez satisfaisants.

En augmentant la précision théorique, on obtient des chiffres quasiment continus permettant d'obtenir la figure \ref{sudoku_points}.

\begin{figure}[!h]
 \center
 
 \caption{Grille de sudoku en point par point tracée avec \emph{MatplotLib}}
 \label{sudoku_points}
\end{figure}

Il faut prévoir dans le script la possibilité d'envoyer une impulsion au servomoteur afin qu'il lève le stylo lorsqu'un chiffre a été tracé afin d'éviter que les chiffres ne soient reliés entre eux, comme le suggère la figure \ref{sudoku_trace}.

\begin{figure}[!h]
 \center
 
 \caption{Grille de sudoku tracée avec \emph{MatplotLib}}
 \label{sudoku_trace}
\end{figure}

\newpage
\subsection*{Connexion entre la Raspberry Pi et un ordinateur distant}
Une Raspberry Pi peut être utilisée comme un véritable ordinateur, il suffit pour cela de lui brancher un écran et un clavier. Le problème de cette utilisation réside dans l'utilisation de l'écran, en effet la \emph{Raspberry Pi} dispose d'une sortie HDMI sur laquelle se branche l'écran. Cependant l'utilisation de cette sortie sur notre bras n'aurait pas du tout été pratique et nous n'avions pas forcément un écran à disposition. C'est pour cela que nous avons développé la possibilité de contrôler la \emph{Raspberry Pi} via une connection sécurisée, le \emph{SSH} (\emph{Secure Shell}). Cependant ce type de connection ne permet pas l'échange d'informations directes entre les deux appareils mais permet de prendre la main à distance sur la \emph{Raspberry} (permettant par exemple d'exécuter des scripts à distance).

C'est pour cela que nous avons utilisé un module python appelé \emph{socket} qui permet l'échange d'informations entre un serveur et un client. Lors de la mise sous tension de la \emph{Raspberry Pi}, plusieurs de nos scripts, à savoir le script principal et le script qui démarre le serveur, sont automatiquement exécutés. Sur le PC distant, il suffit de démarrer l'interface graphique, qui est alors un client pouvant se connecter au serveur de la \emph{Raspberry}. Dans le menu édition, le bouton \emph{Envoyer}\footnote{Cf Figure \ref{Menu_edition} à la page \pageref{Menu_edition}} permet de transmettre la grille courante à la \emph{Raspberry} qui va se charger de l'écrire physiquement. L'écran LCD sert alors à vérifier que les informations ont bien été transmises.

\chapter*{Conclusion}
\addcontentsline{toc}{chapter}{Conclusion}
Ce TIPE a été très bénéfique et nous a tout d'abord permis d'améliorer les compétences acquises l'an dernier en Python.

De plus, de nombreuses nouvelles compétences ont du être mises en œuvre :

\begin{itemize}[label=--]
\item le contrôle de moteurs à l'aide d'une Raspberry Pi
\item la conception de pièces en 3D

\end{itemize}
Tous les scripts et ce dossier sont disponibles sur GitHub\footnote{Sudoku Plotter - \url{www.github.com/alphter/Sudoku-Plotter/}}

\chapter*{Remerciements}
\addcontentsline{toc}{chapter}{Remerciements}

Nous remercions M. Couvez pour ses précieux conseils et Tristan Vajente pour les impressions de pièces en 3D.

%\include{annexe}

\end{document}

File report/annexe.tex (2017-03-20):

\printbibliography
\nocite{*}
\appendix

\begin{changemargin}{-2cm}{-4cm}

\addcontentsline{toc}{chapter}{Scripts Python}
\label{Scripts}
\chapter*{Script principal}
\label{main}
\inputminted[fontsize=\scriptsize, linenos=true]{Python}{../script/main.py}

\chapter*{Script de résolution des sudokus}
\label{resolution}
\inputminted[fontsize=\scriptsize, linenos=true]{Python}{../script/resolution.py}

\chapter*{Script de gestion de la caméra}
\label{camera}
\inputminted[fontsize=\scriptsize, linenos=true]{Python}{../script/camera.py}

\chapter*{Script d'affichage du sudoku}
\label{display}
\inputminted[fontsize=\scriptsize, linenos=true]{Python}{../script/display.py}

\chapter*{Script de gestion des moteurs pas-à-pas}
\label{step_motor}
\inputminted[fontsize=\scriptsize, linenos=true]{Python}{../script/step_motor.py}

\chapter*{Script permettant l'écriture d'un sudoku}
\label{write}
\inputminted[fontsize=\scriptsize, linenos=true]{Python}{../script/write.py}

\addcontentsline{toc}{chapter}{Mises en plan des pièces conçues en 3D}

\chapter*{Mise en plan du chariot}

\begin{figure}[!h]
\label{chariot}
 \center
 
\end{figure}

\chapter*{Mise en plan du support du stylo}
\begin{figure}[!h]
\label{supportstylo}
 \center
 
\end{figure}

\chapter*{Mise en plan du lien chariot/caméra}
\begin{figure}[!h]
\label{chariotcamera}
 \center
 
\end{figure}

\chapter*{Mise en plan du support de la caméra}
\begin{figure}[!h]
\label{supportcamera}
 \center
 
\end{figure}

\end{changemargin}

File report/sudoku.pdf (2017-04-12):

### Institut Supérieur

### d’Électronique de Paris

## TIPE

# Bras mécanique et sudoku

# Laurent Tainturier & Alphonse Terrier

### supervisé par

### M. Patrick COUVEZ

2016-2017

# Table des matières

Introduction | 1
1 Présentation et faits sur le sudoku | 3
2 Mécanique | 4
3 Électronique | 9
4 Informatique | 15
Conclusion | 27
Remerciements | 28

# Introduction

1

1. Sauf mention contraire, les images et figures ont été réalisées par nos soins.

# Chapitre 1

# Présentation et faits sur le sudoku

Le sudoku est un jeu sous forme de grille inspiré du carré latin et défini en 1979 par Howard Garns.
Cette grille est carrée et est divisée en n

2
régions de n

2
cases. Elle possède
ainsi n

2
colonnes, n

2
lignes et n

4
cases. Dans la version la plus commune : n = 3. On appelle section, une ligne, une colonne ou une région
Une grille de sudoku est préremplie, le but du jeu étant de la compléter selon la règle suivante :

– Chaque section doit contenir au moins une fois tous les de 1 à n

2

Une grille est considérée comme sudoku seulement si sa solution est unique. Le minimum de cases remplies au préalable pour espérer que la dite solution soit bien unique est de 17, cela a été prouvé par une équipe islandais en 2012.

# Chapitre 2

# Mécanique

## 2.1 Choix concernant la structure du bras

La premier défi qui s’est imposé à nous a été le choix d’une structure adéquate : solide et pratique. Notre choix s’est alors porté sur les Makerbeam. MakerBeam est un système de construction Open-Source basé sur des profilés ALU en T.
L’écriture se fera en coordonnées polaires et non pas en coordonnées cartésiennes pour les raisons suivantes :

– un système en coordonnées cartésiennes aurait été trop encombrant et un moins "portable" (dans un contexte notamment d’optimalité, comme exigé par le programme)

– c’est un défi technique de fabriquer un bras de ce type en coordonnées polaires

Ainsi, un moteur pas-à-pas assurera la rotation θ du bras. Ce moteur s’autoentrainera autour d’une roue dentée de 128 dents comme celle-ci et un roulement permettra la rotation de l’entièreté du bras :


Figure 2.1 – Schéma de la roue dentée

De même la translation r a été assurée par un deuxième moteur pas-à-pas et un système courroie/poulie. Cette translation s’est faite le long de deux axes de 272 mm et de 8 mm de diamètre.

## 2.2 Étude cinématique du mécanisme

La pièce 0 correspondra par la suite au bâti. La base du bras et le bâti seront supposés en liaison encastrement, alors qu’ils sont en réalité en liaison appui-plan, cependant les forces de frottements entre ces deux pièces sont telles quelles sont presque immobiles l’une par rapport à l’autre. La pièce 1 correspond à la structure du bras, reposant sur la roue dentée. La pièce 2 symbolise le chariot et la pièce 3 le stylo.


Figure 2.2 – Schéma cinématique du mécanisme choisi


Figure 2.3 – Graphe de structure du mécanisme choisi

Les deux liaisons en parallèle entre 2 et 3 peuvent être remplacés par une liaison équivalent ede torseur {Tc(2/3)} devant vérifier l’équation suivante : :

{Tc(2/3)}B = {T

0
c

(2/3)}B = {T

00
c

(2/3)}B

On notera les liaisons entre les pièces 2 et 3 L

0
2/3

et L

00
2/3

. On a alors :

{T

0
c

(2/3)} =

∀P ∈(B,−→z )

0 | 0
0 | 0
γ

0
2/3 | w
| 0
| 2/3
x,y,z)

{T

00
c

(2/3)} =

∀P ∈(C,−→z )

0 | 0
0 | 0
γ

00
2/3 | w
| 00
| 2/3
(x,y,z)

Or −→V (B ∈ 2/3) = −→V (C ∈ 2/3) + −→Ω (2/3) ∧ −−→CB

= w

00
2/3

−→z + γ
00
2/3

−→z ∧ BC−→x

= w

00
2/3

−→z + γ
00

2/3BC−→y

On a donc {T

00
c

(2/3)} =

B

0 | 0
0 | γ
| 00
| 2/3BC
γ

00
2/3 | w
| 00
| 2/3
(x,y,z)

Donc {Tc(2/3)} =

B

0 | 0
0 | 0
γ

0
2/3 w

0
2/3
x,y,z)

=

B

0 | 0
0 | γ

00
2/3BC
γ

00
2/3 w

00
2/3
(x,y,z)

D’où le système d’équation :

0 = 0
0 = 0
γ

0
2/3 = γ

00
2/3
0 = 0
γ

00
2/3 = 0
w

0
2/3 = w

00
2/3

On en déduit {Tc(2/3)} =

B

0 | 0
0 | 0
0 w
| 0 2/3
x,y,z)

La liaison équivalente est donc une liaison glissière d’axe z, ce qui permet des déplacements verticaux du stylo, il peut ainsi être mis en contact avec la feuille. On a alors le schéma de la figure 2.4.


Figure 2.4 – Schéma cinématique équivalent au mécanisme choisi

## 2.3 Difficultés rencontrées et solutions mises en place

Nous avons notamment rencontré des difficultés concernant le roulement utilisé. En effet, nous avions au préalable utilisé un roulement à billes comme celui-ci :

Figure 2.5 – Roulement défectueux

Malheureusement, ce roulement tournait très mal et saccadait. De plus, du jeu était présent. Après quelques heures de recherche, nous avons donc choisi le roulement à billes suivant, qui tourne très bien mais qui tout de même possède lui aussi un peu de jeu :


Figure 2.6 – Roulement finalement choisi

## 2.4 Conception du chariot en 3D

Nous avons pris la décision de concevoir certaines pièces de notre projet en 3D, celle-ci nécessitant de la précision. Le logiciel professionnel de modélisation SolidWorks, développé par DassaultSystèmes, a été utilisé pour développer ces pièces.
Les mises en plan des pièces composant le chariot sont disponibles en annexe ?? à partir de la page ??.
La partie principale du chariot devait pouvoir accueillir un servomoteur, permettant l’abaissement et le soulèvement du stylo :
Ce stylo sera fixé sur la pièce présentée en page ?? dont l’impression 3D est montrée ci-dessous :
L’ensemble chariot/support du stylo imprimé en 3D est alors montrée ci-dessous :

Le chariot permet, de façon modulaire, d’accueillir un support caméra se divisant en deux pièces présentées en page ?? et en page ??.

# Chapitre 3

# Électronique

## 3.1 Moteurs pas-à-pas

Nous avons utilisé dans ce projet deux moteurs pas-à-pas qui présentaient, par rapport à d’autres types de moteurs, les avantages suivants :

– une précision bien supérieure à celle de moteurs à courant continu ;

– un couple bien plus important que celui de servomoteurs ;

– mis sous tension, un déplacement fortuit du moteur n’est pas possible.

Les moteurs pas-à-pas sont notamment utilisés dans les systèmes nécessitant une grande précision comme les imprimantes 3D dans lesquelles ils sont très largement employés.


Figure 3.1 – Schéma simplifiée d’un moteur pas-à-pas ¹

Les moteurs que nous avons utilisés sont constitués de deux bobines, repliées tout autour de la partie centrale du moteur, permettant des petits déplacements de la partie mobile. Celles-ci sont divisées en deux sur la figure 3.1. La bobine 1 a pour extrémités A et B ; la bobine 2 C et D. Ces bobines, lorsqu’elles

1. http://eskimon.fr/290-arduino-603-petits-pas-le-moteur-pas-pas sont parcourues par un courant i, génèrent un champ magnétique. Ce champ magnétique a pour conséquence d’entrainer la rotation de la partie mobile du moteur : le rotor, représenté par le cercle centrale N/S. Celui-ci est composé d’un aimant qui a tendance a s’aligner sur le champ magnétique créé par les bobines. Les bobines sont enroulées autour d’un fer doux, généralement de la ferrite afin de mieux conduire le lignes de champs.

On distingue deux types de fonctionnement pour ces moteurs bipolaires, un fonctionnement à demi-pas et un fonctionnement à pas complet. Nous avons retenu ce dernier système car il permettait d’obtenir une vitesse et un couple constants lors de la rotation des moteurs. Comme le montre la figure 3.2, à chaque séquence, une seule bobine suffirait à mettre en mouvement le moteur, cependant nous avons choisi d’alimenter tout de même l’autre afin d’obtenir un couple maximal (cf figure 3.3).

Séquence | Bobine 1 | Bobine 2
A | B | C | D
1 | 1 | 0 | - | -
2 | - | - | 0 | 1
3 | 0 | 1 | - | -
4 | - | - | 1 | 0
5 | 1 | 0 | - | -

Table 3.1 – Séquences d’alimentation des bobines avec un couple minimal

Séquence | Bobine 1 | Bobine 2
A | B | C | D
1 | 1 | 0 | 0 | 1
2 | 0 | 1 | 0 | 1
3 | 0 | 1 | 1 | 0
4 | 1 | 0 | 1 | 0
5 | 1 | 0 | 0 | 1

Table 3.2 – Séquences d’alimentation des bobines avec un couple maximal


Figure 3.2 – Fonctionnement à pas complet avec un couple minimal ²


Figure 3.3 – Fonctionnement à pas complet avec un couple maximal ³

Une autre différence entre l’alimentation d’une ou deux bobines réside dans la position de l’axe des deux moteurs, la position de celui-ci est décalé d’un demi-pas. Le fonctionnement en demi-pas se base ainsi sur la combinaison de ces deux méthodes, ce qui entraîne un couple variable mais permet des déplacements plus précis.

## 3.2 Drivers L293D

Pour piloter les moteurs, nous utilisons des drivers L293D. Ces drivers présentent les avantages suivants :

– ils permettent l’utilisation d’une source de tension externe, la Raspberry ne pouvant fournir que du 5V ;
– ils intègrent deux ponts en H permettant d’inverser le courant circulant dans les bobines ;
– ils permettent d’éviter la création de courants induits dans la Raspberry, du faits des bobines, pouvant potentiellement l’endommager ou la détruire.


Figure 3.4 – Utilité du pont en H, réalisé avec QElectroTech

2. Une animation du pas complet avec couple minimal est disponible sur www.github. com/alphter/Sudoku-Plotter/blob/master/pictures/motor_min1.gif
3. Une animation du pas complet avec couple maximal est disponible sur www.github. com/alphter/Sudoku-Plotter/blob/master/pictures/motor_max1.gif

Les ponts en H permettent l’alimentation d’une bobine dans les deux sens, ils permettent également de freiner le moteur en le court-circuitant. Celui-ci est constitué de quatre interrupteurs, conformément à la figure 3.5. Le moteur M représente une bobine. Les ponts en H sont utilisés dans quasiment tous les drivers des moteurs, que ce soit des moteurs continus ou des pas-à-pas. Les interrupteurs sont alors remplacés par des transistors, ce qui permet de les commander par une autre source d’alimentation (par exemple du 5V). Pour éviter la création de courants induits dans les bobines, on place généralement des diodes en parallèle des transistors (ou des interrupteurs).


Figure 3.5 – Pont en H intégré dans les drivers, réalisé avec QElectroTech

Le driver L293D présente l’avantage d’intégrer deux pont en H ainsi que les diodes en parallèle ce qui permet des branchements aisés, sans besoin d’ajout d’autres composants. Comme nos moteurs intègrent deux bobines chacun, nous avons eu besoin de deux L293D, un par moteur.

## 3.3 Schéma électrique

Le schéma ci-joint représente les principales connections au sein de notre montage, même s’il ne présente ni l’écran LCD, ni le détail de l’alimentation de la Raspberry Pi (notamment du convertisseur de tension).
Les moteurs deux bobines de chaque moteur sont reliées aux deux drivers l293D . Ceux-ci sont pilotés par quatre sorties GPIO qui envoient des impulsions au driver qui alimente les bobines en 12V à tour de rôle, ce qui permet à la fois de contrôler le sens et la vitesse de de rotation des moteurs, en choisissant à quelle fréquence envoyer les impulsions. La figure 3.6 souligne la présence de deux alimentations différentes, à la fois l’alimentation 5V pour la Raspberry Pi et l’alimentation 9V(ou 12V) pour alimenter les moteurs.


Figure 3.6 – Schéma électrique réalisé avec Fritzing

## 3.4 Premiers montages

Nous avons réalisés nos premiers montages avec une breadboard facilitant les tests. Une simulation du schéma a également été réalisée sous Fritzing :


Figure 3.7 – Premier montage réalisé avec Fritzing

## 3.5 Circuit imprimé

Pour rendre notre bras mécanique plus compact et ainsi rentrer dans le cadre de l’optimalité, nous avons souhaité remplacer la breadboard par une solution bien plus compacte, à savoir un circuit imprimé. Celui-ci sera enficher directement sur les ports GPIO de la Raspberry Pi. Nous avons de nouveau utilisé pour le réaliser le logiciel Fritzing, permettant la réalisation du circuit sur deux couches (symbolisées par les couleurs orange et jaune), permettant un cablage plus facile, car autorisant les croisements. Nous avons utilisé Fritzing car il été assez facile de faire faire fabriquer le circuit imprimé pour une dizaine d’euros. Nous avions hésité à réaliser entièrement ce circuit par nous même, mais du fait de la présence des deux couches, cela se serait révélé très difficile et aurait sans doute coûté plus cher.


Figure 3.8 – Circuit imprimé réalisé avec Fritzing

## 3.6 Écran LCD

Pour rendre le bras mécanique plus autonome, nous avons intégré un écran LCD permettant à l’utilisateur de se repérer dans l’évolution des différents scripts sans disposer nécessairement d’un ordinateur ou d’un écran à proximité, ce qui permettait une utilisation facilitée de celui-ci. L’écran utilisé est un écran LCD 2x16, disposant d’un potentiomètre intégré permettant de régler la luminosité de l’écran. Il dispose de quatre sorties, à savoir une sortie 5V, la masse et deux sorties pour envoyer les informations.


Figure 3.9 – Écran LCD affichant le message de bienvenue

# Chapitre 4

# Informatique

## 4.1 Présentation globale

Tous les algorithmes développés dans le cadre de ce projet sont disponibles en annexe. Ils ont été, pour la plupart, développés sous Python 3, les autres sous Python 2 car certaines bibliothèques dont nous avions besoin, notamment pour la reconnaissance, n’était disponible que sous Python 2.
Nous avons développé une programmation modulaire, permettant de travailler simultanément sur le projet, sans pour autant poser de problème de logistique. Ainsi nous avons dissocié tous les scripts ; que ce soit la reconnaissance, la résolution, l’affichage, la gestion de la caméra ou des moteurs, etc. Pour cela, nous avons développé une relation qualifiable de maître-esclave entre nos scripts. Chacun des scripts dépend d’un fichier principal, appelé main, qui récupère les informations des autres scripts et donne les ordres adéquats à ceux-ci, selon la situation. Ainsi, les scripts ne sont pas reliés les uns aux autres mais seulement à ce script principal, ce qui permet d’ajouter ou d’enlever très facilement tel ou tel script, sans pour autant altérer le fonctionnement de l’ensemble, permettant ainsi de tester chacun des scripts très facilement.

## 4.2 Reconnaissance du sudoku

Le script de reconnaissance du sudoku a été réalisé sous Python 2 avec le module de traitements d’image OpenCV. Il a été réalisé pour :

– Reconnaître les chiffres dans une grille du sudoku

– Déterminer la position spatiale de la grille

On photographie la grille avec une caméra Raspberry Pi (V2) comme celle-ci :

Voici la grille de sudoku qui nous servira d’exemple pour montrer toutes les actions du script :

Figure 4.1 – Caméra Raspberry Pi V2


Figure 4.2 – Exemple de grille de sudoku

On applique sur cette photographie un filtre de type seuil (en anglais "threshold") qui va ensuite nous permettre de détecter les contours de la grille :


Figure 4.3 – Exemple de grille "seuillée"

Par cette transformation, on peut ensuite déterminer des équations de droites des contours extérieurs de la grille. Les coordonnées des intersections des droites seront celle des coins de la grille.
On découpe alors la grille de la photographie initiale en supprimant les éventuels effets de perspective.


Figure 4.4 – Exemple de grille découpée sans perspective

On découpe chaque petite case de la grille comme ci-dessous :


Figure 4.5 – Exemple de grille où chaque chiffre a été découpé

On utilise ensuite un module de reconnaissance de digits pour détecter les chiffres et on obtient la grille suivante, prête à être résolue :


Figure 4.6 – Exemple de grille prête à être résolue

## 4.3 Résolution du sudoku

Pour résoudre une grille de sudoku, un joueur utilise différentes méthodes de résolution, qui sont purement algorithmiques. Il utilise en grande majorité deux méthodes qui peuvent permettre de résoudre une grande partie des grilles disponibles sur le marché. On appelle ces deux méthodes inclusion et exclusion. Cependant les grilles de niveau supérieur font appel à des méthodes plus subtiles et souvent plus difficiles à appliquer en pratique qui se basent généralement sur des paires ou des triplets. Les grilles les plus difficiles peuvent imposer au joueur de faire un choix entre plusieurs possibilités pour espérer mener à son terme la résolution. C’est sur ce constat que ce base la méthode dite de backtracking (ou retour sur trace), qui permet de résoudre toute grille de sudoku, même si celle-ci n’est pas valide et possède plusieurs solutions. Bien sûr cette liste n’est pas exhaustive et il existe d’autres méthodes de résolution, même si ces méthodes ne sont pas forcément très employées et faciles d’emploi.

Inclusion : un seul candidat pour une case On dénombre pour chaque case vierge les chiffres pouvant être positionnés dans celle-ci. S’il n’y a qu’une seule possibilité alors elle est solution et est donc placée dans la case.

Figure 4.7 – Méthode d’inclusion pour une région

Exclusion : candidat unique pour une section Si pour un chiffre donné, on ne peut le placer dans une section que dans une seule case possible, alors ce chiffre est placé dans cette case

Figure 4.8 – Méthode d’exclusion pour une région

Paires Si dans une section donnée, deux cases ne contiennent que deux candidats identiques, alors ils ne peuvent être placés que dans ces deux cases, ce qui permet de les éliminer des autres possibilité pour la section

Figure 4.9 – Méthode des paires pour une ligne

La méthode des triplets est une généralisation de cette méthode à trois cases et non seulement deux.

Jumeaux Si dans une section, un chiffre ne peut être placé que sur une ligne (resp. colonne), alors ce chiffre peut être supprimé des possibilités pour le reste de la ligne (resp.colonne). Cette méthode ne permet pas toujours de placer immédiatement celui-ci, mais permet de réduire les possibilités pour placer les autres.

Figure 4.10 – Méthode des jumeaux pour une ligne

Backtracking Cette méthode ¹
consiste tout d’abord à lister pour chacune des cases vierges les chiffres qui pourraient correspondre. On part d’une case vierge quelconque qu’on remplit par un des chiffres pouvant théoriquement convenir, puis on liste les nouvelles possibilités des autres cases en fonction du chiffre précédemment ajouté puis on passe à la case suivante. S’il n’y a plus aucune possibilité, on revient sur nos pas et on change le chiffre qu’on venait d’ajouter en une autre possibilité. Si tout les chiffres possibles ont été testé, on revient de nouveau sur nos pas autant de fois que nécessaire, jusqu’à avoir compéter la totalité de la grille.
1. Une animation du backtracking est disponible sur : www.github.com/alphter/ Sudoku-Plotter/blob/master/pictures/backtracking.gif

Partant de ce constat, nous avons tout d’abord implémenté la méthode de backtracking, ainsi, il nous était possible de résoudre toutes les grilles possibles. À l’origine, notre algorithme parcourait la grille dans un ordre prédéfini, à savoir de haut en bas et de gauche à droite. Cependant, il pouvait arriver que pour certaines grilles, ce système n’était pas tout à fait optimale. C’est pourquoi, nous l’avons changé de sorte que l’algorithme commence par les cases présentant le moins de possibilités, permettant dans le cas général de diminuer le temps de résolution. Cependant, dans le pire des cas, cette solution ne présentait aucune différence en terme de temps de calculs.

Temps de calculs Au niveau informatique, ces méthodes ne se valent pas dans la mesure où elles sont plus ou moins fiables, efficaces et rapides. L’inclusion et l’exclusion sont comparables : elles sont rapides et efficaces mais ne permettent pas la résolution complète dans un certain nombre de cas. L’utilisation du backtracking se révèle alors efficace en complément des deux précédentes, puisque cette méthode permet toujours de conclure. Les temps de calculs sont comparables pour toutes ces méthodes et sont de l’ordre du centième de secondes ²
. La résolution peut parfois prendre plus d’une seconde mais cette situation ne s’est présentée que très rarement. Cependant, il peut arriver que pour des grilles très particulières, conçues pour tester la rapidité du backtracking, la résolution du sudoku prenne bien plus de temps, jusqu’à 30 secondes. En utilisant les trois méthodes de manière couplée, le temps de calculs diminue pour arriver à seulement 20 secondes. Une utilisation couplée des méthodes est bien plus efficace car permet d’éliminer immédiatement toutes les possibilités évidentes, indétectables en backtracking, pour ensuite l’utiliser éventuellement si la grille n’est pas résolue.
2. Les résultats peuvent varier d’un machine à l’autre comme nous avons pu le constater, il est donc surtout intéressant de noter les différences d’ordres de grandeurs entre les différents résultats.

## 4.4 Interface graphique

Pour rendre la résolution plus simple d’utilisation, nous avons décidé d’ajouter une interface graphique. Le cahier des charges qu’elle devait vérifier était assez stricte. Elle devait pouvoir afficher, avant toute chose, une grille de sudoku qui devait dès lors être facilement modifiable. Pour cela, nous avons donc créé différents menus ; l’un permettant donc l’édition de la grille, un autre permettant de choisir la méthode de résolution, ainsi qu’un menu de résolution.


Figure 4.11 – Interface graphique du Sudoku

Édition Lors de l’édition de la grille, un carré rouge apparait, déplaçable avec les flèches directionnelles, il suffit alors pour modifier la case de rentrer un chiffre de 0 à 9, 0 correspondant à une case vierge. Il est également possible de sauvegarder une grille ou encore de récupérer une grille déjà enregistrée.


Figure 4.12 – Menu Édition de l’interface graphique

Résolution Ce menu permet de lancer la résolution, et permet également de choisir entre une résolution rapide ou une résolution pas-à-pas permettant à l’utilisateur d’observer le fonctionnement de ces algorithmes.

Figure 4.13 – Menu Résolution de l’interface graphique

Méthode Le choix de la méthode se fait avec le menu Méthode, qui permet de choisir la méthode de résolution parmi l’inclusion, l’exclusion et le backtracking ou de choisir une méthode dite globale, s’appuyant sur tous ces algorithmes, permettant ainsi d’être la plus rapide possible.

## 4.5 Contrôle des moteurs et écriture

### Moteurs pas-à-pas

Il nous apparaissait nécessaire de développer une programmation permettant l’exécution simultanée de plusieurs instructions, notamment pour les moteurs. En effet, les moteurs doivent absolument fonctionner de manière synchrone afin d’obtenir des déplacements les plus précis possibles. C’est pour cela que nous nous sommes basés sur ce qui pourrait être qualifiée de "programmation parallèle" qui permet l’exécution de plusieurs processus simultanément. Cela est rendu possible en Python par l’utilisation de la bibliothèque threading depuis laquelle nous utilisons Thread (signifiant processus en français). Pour piloter les moteurs, il suffit d’envoyer des impulsions dans les bobines pour faire tourner les moteurs dans le bon sens. La fréquence d’envoi de ces impulsions conditionne la vitesse des moteurs. Les impulsions doivent être envoyés au maximum toute les 10 ms, ce qui constitue la vitesse maximum des moteurs. Ces impulsions sont envoyés au deux moteurs de manière cycliques, un cycle étant constitué de quatre séquences ³
. Le script d’écriture des digits transmet à celui des moteurs une liste des coordonnées des points à parcourir. Ces coordonnées sont ensuite converties en déplacements élémentaires pour les deux moteurs, ce qui se traduit alors en impulsions et permet les déplacements des moteurs.
3. cf section 3.1 à la page 9

### Coordonnées polaires

Par soucis de compacité et ainsi s’inscrire dans l’optimalité du programme, nous avons décidé de développer une structure se basant sur les coordonnées polaires, permettant des dimensions maximum de 40 par 10 cm. L’utilisation de telles coordonnées nécessitait une plus grande précision et relevait donc d’un plus grand défi technique. Les coordonnées polaires ne sont de plus, que très peu utilisés pour ce type de système, ce qui nous à incité à développer une structure se basant sur ces coordonnées.


Figure 4.14 – Changement de repères réalisé avec Geogebra

Sur la figure 4.14, le point O1 correspond au centre de la roue dentée. Le point A correspond à la position du bras et le point B correspond à la position que l’on souhaite atteindre. On peut noter que le bras doit pivoter d’un angle θ = 0.74 rad et doit se déplacer d’une distance algébrique r pour atteindre ce point B. Ces deux données sont transmises aux moteurs qui vont se déplacer d’un nombre de pas équivalent pour l’un à θ et pour l’autre à r. On comprend alors qu’il faut suffisamment de points pour éviter de tracer des lignes courbes, en effet si A et B se situent à la même distance du centre O1, le stylo tracera un arc de cercle Pour avoir accès à θ et r, il faut convertir les coordonnées des point A et B en coordonnées polaires de centre O1. On notera xA et yA les coordonnées cartésiennes du point A et rA et θA ses coordonnées polaires de centre O1. Les coordonnées du point O1 seront eux indicées par 0. On a alors :

xA = rA · cos θ + x0

yA = rA · cos θ + y0

et

rA =

q
(xA − x0)

2 + (yA − y0)
2

θA =

yA−y0
|yA−y0|
- arccos

yA − y0
rA

Comme rA = 0 ⇐⇒ A = O1 et que A est un point de la feuille alors que O1 ne l’est pas, rA ne peut être nul ⁴
. On en déduit que θA est bien définie quelque soit A. En notant nbstep1 (resp. nbstep2) le nombre de déplacements élémentaires du moteur 1 (resp. du moteur 2), on obtient :

r = rB − rA

θ = θA − θB

et

nbstep1 = E(

r
rstep

+

1/2)

nbstep2 = E(

θ
θstep

+

1/2)

Les entiers relatifs nbstep1 et nbstep2 sont les deux informations véritablement importantes pour les moteurs et qui correspondent aux nombre de séquences de leurs déplacements.

### Écriture des digits

Nous souhaitions dès le début pouvoir écrire des grilles de différentes tailles, et non des grilles de tailles fixes. C’est pourquoi nous avons basé le script d’écriture sur du point par point, permettant de choisir la précision théorique des chiffres tracés. Cependant les moteurs pas-à-pas ne pouvant se déplacer que d’un pas fixé de 1.8˚, une trop grande précision ne pourrait entraînerait que des déplacements nuls des moteurs, c’est pourquoi cette manière de programmation permet un compromis entre précision théorique et précision pratique.

Figure 4.15 – Chiffres d’une précision théorique assez faible

Le script permettant de tracer les chiffres prend deux paramètres, à savoir la hauteur des chiffres et la précision attendue. Lors des tests du bras mécanique, ces deux paramètres se sont révélés déterminants pour obtenir le meilleur résultat possible. Les chiffres en tant que tel sont constitués de lignes et d’arc de cercle permettant d’obtenir un résultats assez satisfaisants.
En augmentant la précision théorique, on obtient des chiffres quasiment continus permettant d’obtenir la figure 4.16.
Il faut prévoir dans le script la possibilité d’envoyer une impulsion au servomoteur afin qu’il lève le stylo lorsqu’un chiffre a été tracé afin d’éviter que les chiffres ne soient reliés entre eux, comme le suggère la figure 4.17.
4. De plus, du fait du mécanisme, le point O1 ne peut pas être atteint par le stylo


Figure 4.16 – Grille de sudoku en point par point tracée avec MatplotLib


Figure 4.17 – Grille de sudoku tracée avec MatplotLib

### Connexion entre la Raspberry Pi et un ordinateur distant

Une Raspberry Pi peut être utilisée comme un véritable ordinateur, il suffit pour cela de lui brancher un écran et un clavier. Le problème de cette utilisation réside dans l’utilisation de l’écran, en effet la Raspberry Pi dispose d’une sortie HDMI sur laquelle se branche l’écran. Cependant l’utilisation de cette sortie sur notre bras n’aurait pas du tout été pratique et nous n’avions pas forcément un écran à disposition. C’est pour cela que nous avons développé la possibilité de contrôler la Raspberry Pi via une connection sécurisée, le SSH (Secure Shell). Cependant ce type de connection ne permet pas l’échange d’informations directes entre les deux appareils mais permet de prendre la main à distance sur la Raspberry (permettant par exemple d’exécuter des scripts à distance).
C’est pour cela que nous avons utilisé un module python appelé socket qui permet l’échange d’informations entre un serveur et un client. Lors de la mise sous tension de la Raspberry Pi, plusieurs de nos scripts, à savoir le script principal et le script qui démarre le serveur, sont automatiquement exécutés. Sur le PC distant, il suffit de démarrer l’interface graphique, qui est alors un client pouvant se connecter au serveur de la Raspberry. Dans le menu édition, le bouton Envoyer ⁵ permet de transmettre la grille courante à la Raspberry qui va se charger de l’écrire physiquement. L’écran LCD sert alors à vérifier que les informations ont bien été transmises.
5. Cf Figure 4.12 à la page 21

# Conclusion

Ce TIPE a été très bénéfique et nous a tout d’abord permis d’améliorer les compétences acquises l’an dernier en Python.
De plus, de nombreuses nouvelles compétences ont du être mises en œuvre :

– le contrôle de moteurs à l’aide d’une Raspberry Pi

– la conception de pièces en 3D

Tous les scripts et ce dossier sont disponibles sur GitHub ⁶

6. Sudoku Plotter - www.github.com/alphter/Sudoku-Plotter/

# Remerciements

Nous remercions M. Couvez pour ses précieux conseils et Tristan Vajente pour les impressions de pièces en 3D.

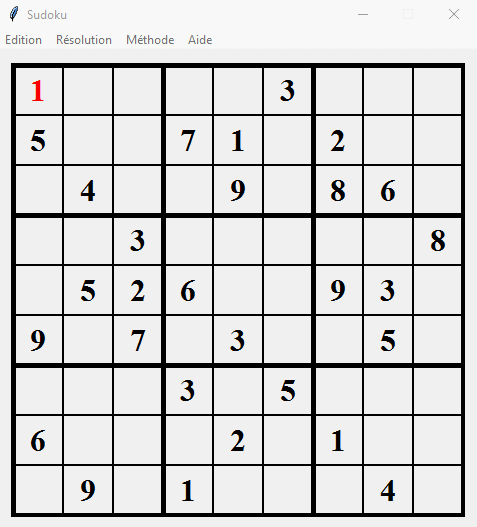
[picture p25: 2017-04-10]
pictures/backtracking/backtracking.gif

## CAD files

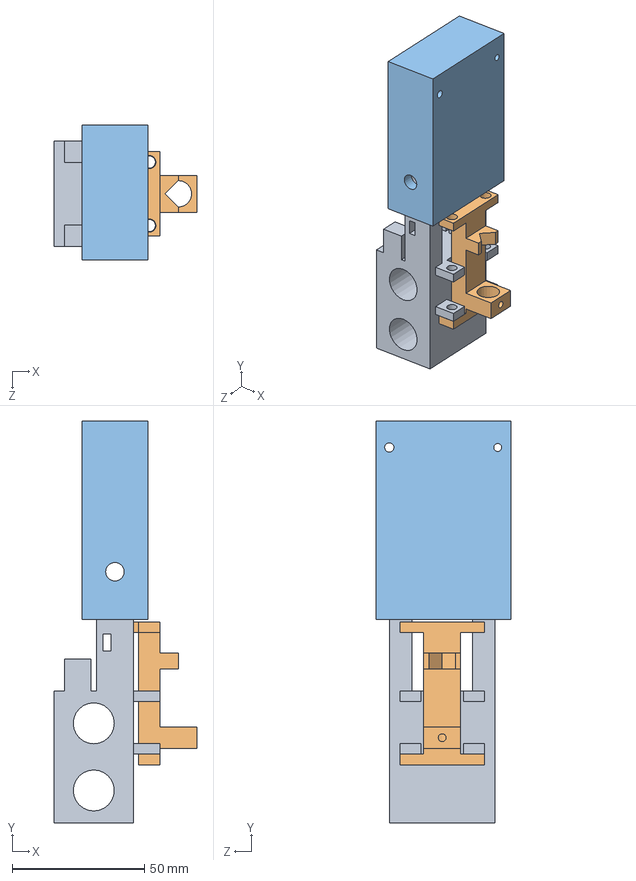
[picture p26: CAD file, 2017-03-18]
3Dmodels/assemblage.SLDASM
54.0 x 152.0 x 51.0 mm
chariot
support stylo
support camera-chariot

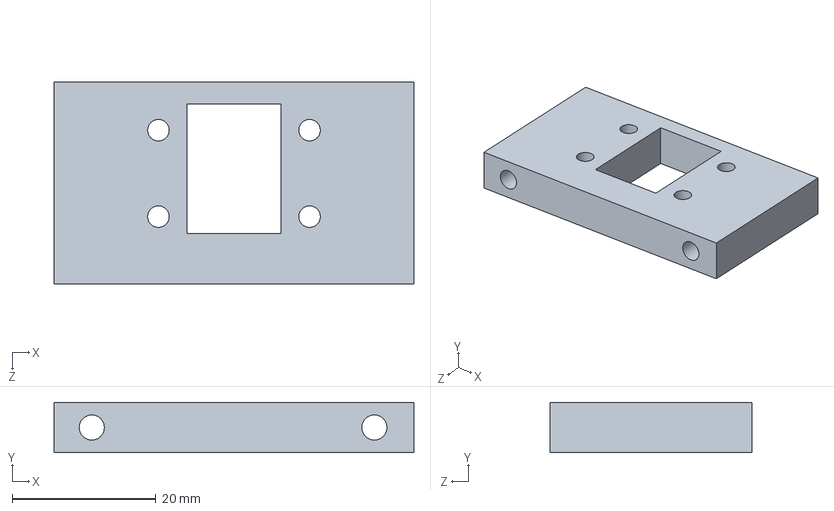
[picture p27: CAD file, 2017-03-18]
3Dmodels/camera.SLDPRT
50.0 x 7.00 x 28.0 mm

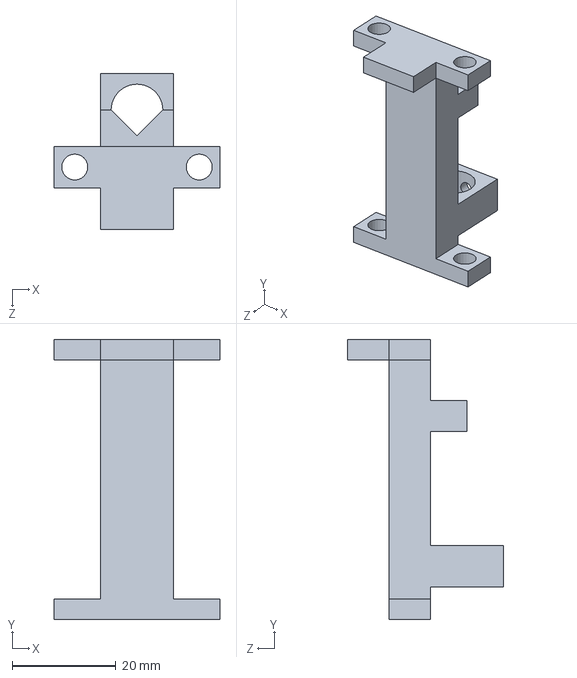
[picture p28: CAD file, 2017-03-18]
3Dmodels/support stylo.SLDPRT
32.0 x 54.0 x 30.0 mm

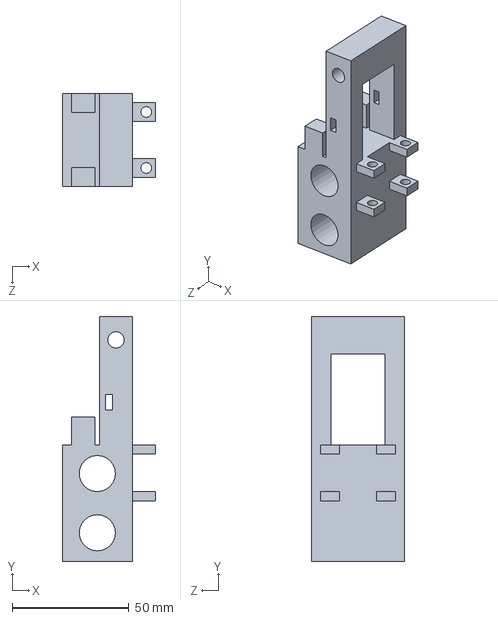
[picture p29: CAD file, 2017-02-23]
3Dmodels/chariot.SLDPRT
40.0 x 105.0 x 40.0 mm

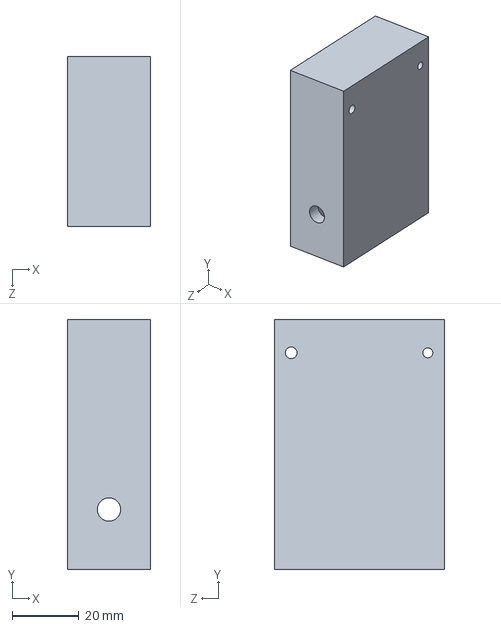
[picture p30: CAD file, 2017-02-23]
3Dmodels/support camera-chariot.SLDPRT
25.0 x 75.0 x 51.0 mm

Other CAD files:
3Dmodels/camera.SLDDRW
3Dmodels/camera.STL
3Dmodels/chariot.SLDDRW
3Dmodels/support camera-chariot.SLDDRW
3Dmodels/support stylo.SLDDRW

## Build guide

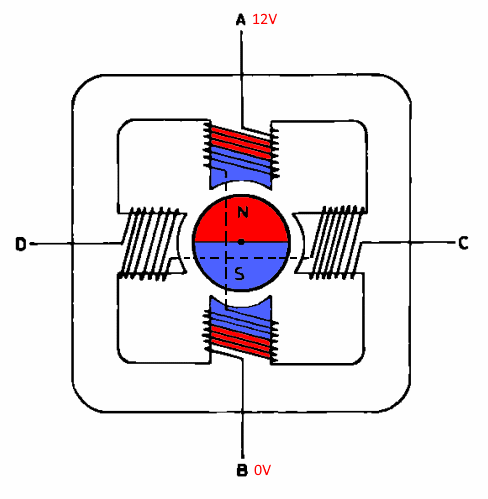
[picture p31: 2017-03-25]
pictures/motor_min_step1.png

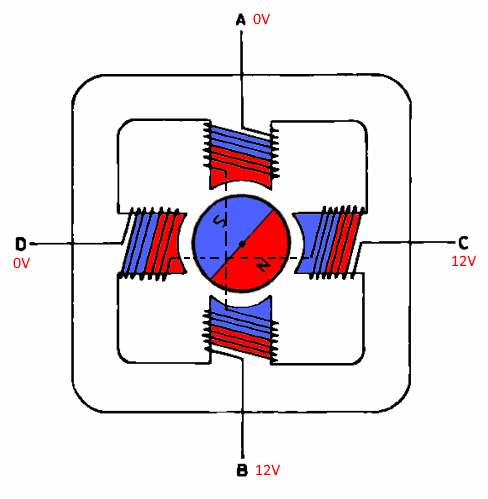
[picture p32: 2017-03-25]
pictures/motor_max_step2.png

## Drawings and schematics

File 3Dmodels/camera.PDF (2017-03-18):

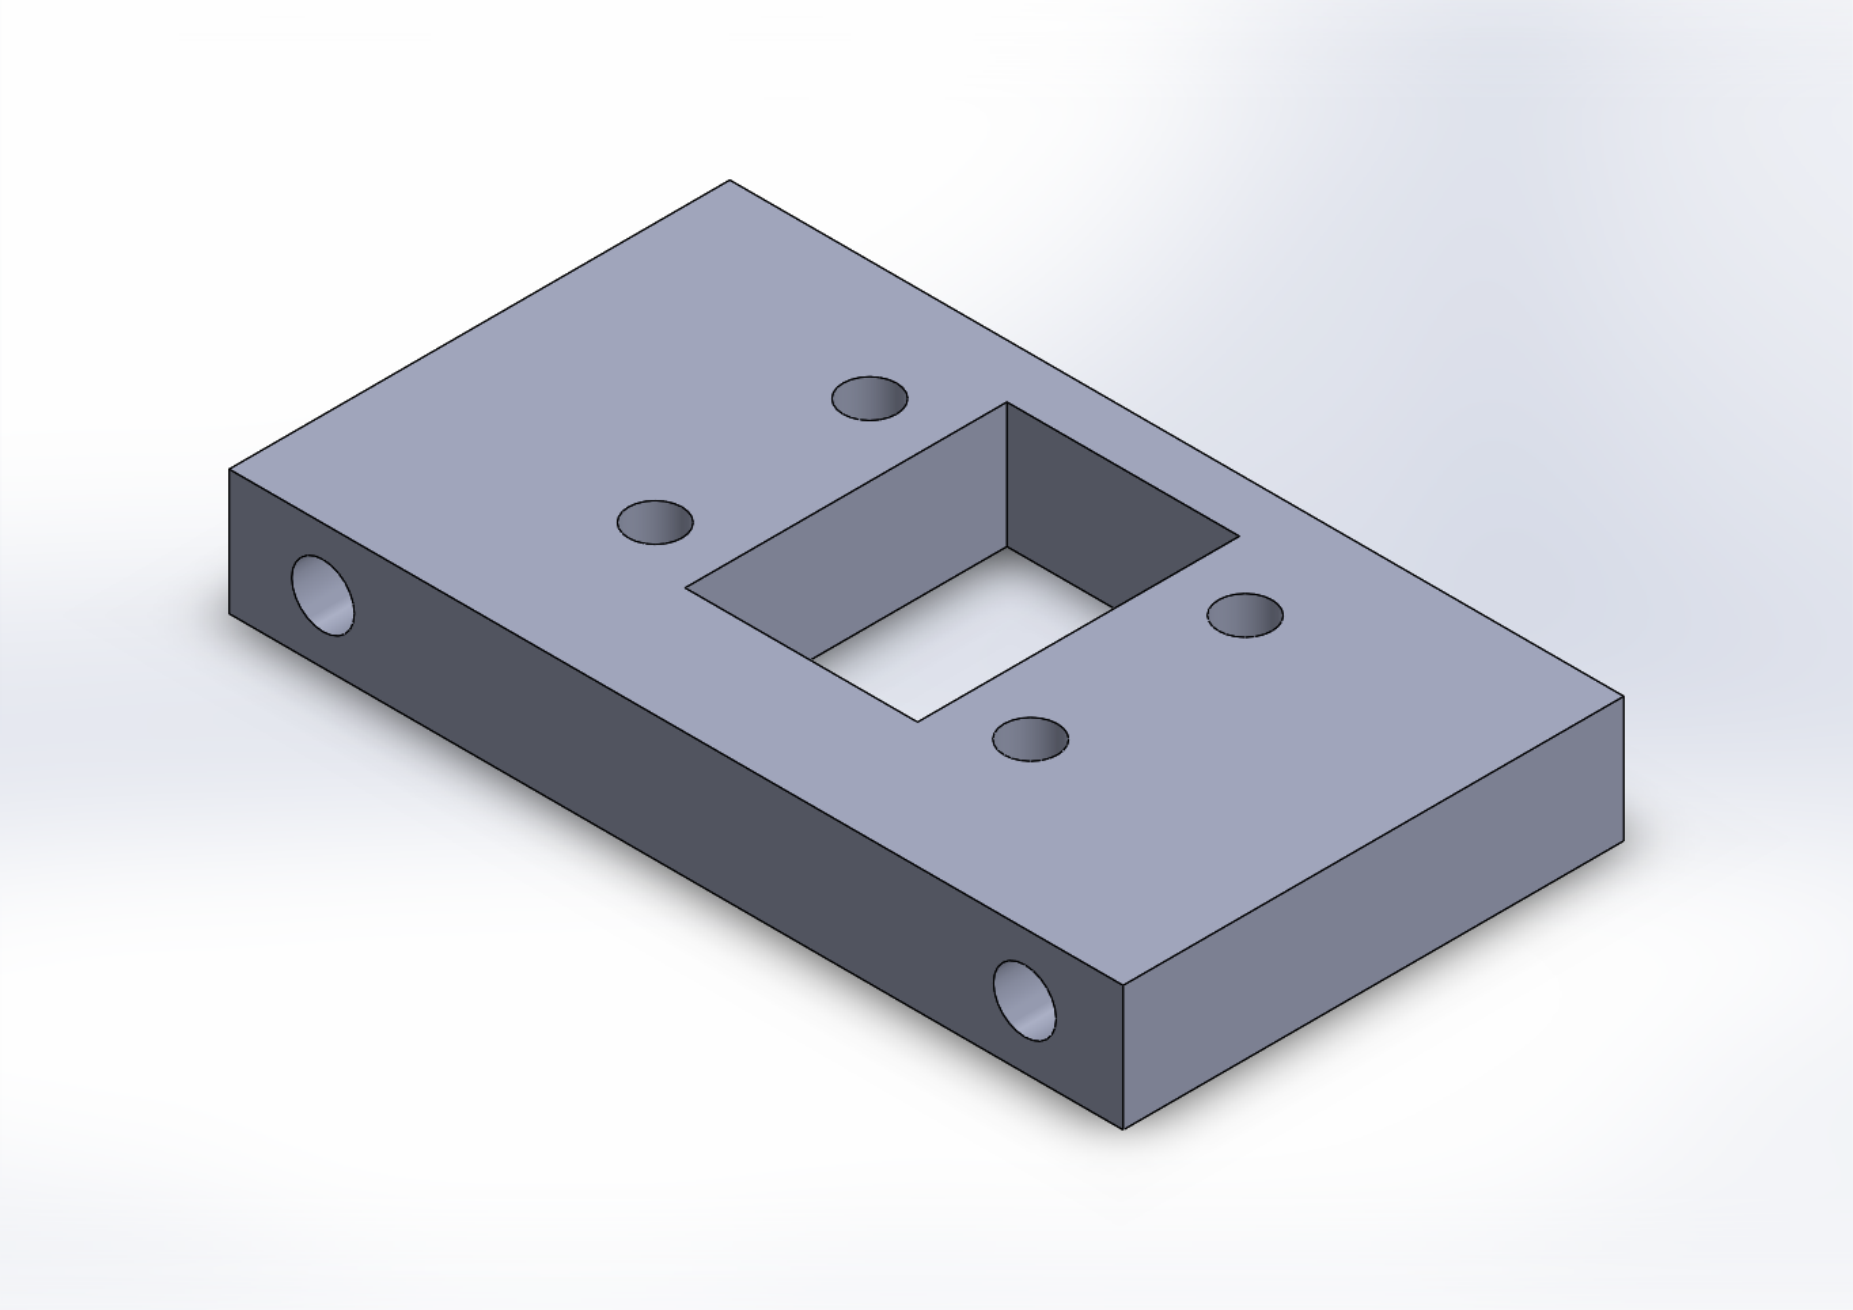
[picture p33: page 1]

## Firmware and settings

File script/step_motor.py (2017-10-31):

#!/usr/bin/env/python3
# -*- coding: utf-8 -*-

import time
import math
import threading

try:
    error = None
    import button as bt
    import RPi.GPIO as GPIO
except ImportError:
    error = "module_GPIO"


class MotorControl(threading.Thread):
    """
    Vérifie que le module RPI.GPIO permettant de gérer les sorties/entrées GPIO
    de la raspberry a été importé correctement,
    définit les sorties GPIO de la Raspberry utilisées pour controler les moteurs,
    initialise les processus des moteurs (motor1 et motor2),
    déplace les moteurs simultanément pour se rendre b'un point à un autre
    """

    def __init__(self):
        threading.Thread.__init__(self)
        self.tryError()
        self.power = True
        self.beta_version = True
        self.bobines_motor1 = (29, 31, 33, 35)
        self.bobines_motor2 = (7, 11, 13, 15)
        self.pwm_servo = 8
        self.sleep_servo = 0.4
        self.up = []
        self.down = []
        self.turn_on_led = 19
        self.working_led = 21
        self.M = Point(0, 7)
        self.max_speed = 0
        self.max_speed1 = 20 / 1000
        self.max_speed2 = 20 / 1000
        self.r_step = 0.0203
        self.theta_step = 0.0056
        self.nb_steps = []
        self.pen_position = []
        self.pinInit()

        self.motor1 = Motor(self.bobines_motor1)
        self.motor2 = Motor(self.bobines_motor2)
        self.servoMotor = ServoMotor(self.pwm_servo)
        self.setMicroStep()
        self.initializePosition()

    def run(self):        
        while self.power:
            self.motor1.checkTime()
            self.motor2.checkTime()
            if not self.motor1.nb_steps and not self.motor2.nb_steps:
                self.writeNextPoints()

    def initializePosition(self):
        self.motor1.initializePosition()

    def writeNextPoints(self):        
        if self.up and not self.up[0]:
            self.servoMotor.setServo("up")
            time.sleep(self.servo_sleep)
            self.up.pop(0)
        elif self.down and not self.down[0]:
            self.servoMotor.setServo("down")
            time.sleep(self.servo_sleep)
            self.down.pop(0)
        else:
            if self.nb_steps:
                self.motor1.nb_steps = self.nb_steps[0][0]
                self.motor2.nb_steps = self.nb_steps[0][1]
                self.nb_steps.pop(0)
                if self.up: self.up[0] -= 1
                if self.down: self.down[0] -= 1
                print(self.nb_steps)
                self.setTime()

    def convertPoints(self, points):
        # <previous_up> (resp. <previous_down>) definissent l'espacement entre deux "up" successifs (resp. "down")
        previous_up = 0
        previous_down = 0

        for i in range(len(points)):
            if points[i] == "up":
                self.up.append(i - previous_up)  # ajout de l'ecart entre deux "up" successifs
                previous_up = i + 1
                previous_down += 1  # permet de ne pas comptabiliser si ce n'est pas un point (ie si point[i] = "up")
            elif points[i] == "down":
                self.down.append(i - previous_down)  # ajout de l'ecart entre deux "down" successifs
                previous_down = i + 1
                previous_up += 1  # permet de ne pas comptabiliser si ce n'est pas un point (ie si point[i] = "down")
            else:
                x, y = points[i]
                B = Point(x, y)
                r = B.r - self.M.r
                theta = B.theta - self.M.theta
                self.nb_steps.append((int(r / self.r_step + 0.5), int(theta / self.theta_step + 0.5)))
                self.M = Point(self.M.r + self.nb_steps[-1][0] * self.r_step,
                               self.M.theta + self.nb_steps[-1][1] * self.theta_step, "polar")

        """for i in range(len(self.points)):
            if self.points[i] != "up" and self.points[i] != "down":
                self.motor1.nb_steps = self.nb_steps1[i]
                self.motor2.nb_steps = self.nb_steps2[i]
                self.motor1.speed = self.speed1[i]
                self.motor2.speed = self.speed2[i]
            else:
                self.servoMotor.setServo(self.points[0])
            while self.motor1.nb_steps != 0 or self.motor2.nb_steps != 0:
                time.sleep(0.0001)"""
        self.sleep()

    def setTime(self):
        """if not self.nb_steps[-1][0]:
            self.motor1.speed.append(0)
            self.motor2.speed.append(self.max_speed2)
        elif not self.nb_steps[-1][1]:
            self.motor1.speed.append(self.max_speed1)
            self.motor2.speed.append(0)
        else:
            total_time1 = abs(self.max_speed1 * self.nb_steps[-1][0])
            total_time2 = abs(self.max_speed2 * self.nb_steps[-1][1])
            if (total_time1 > total_time2 and abs(total_time2 / self.nb_steps[-1][0]) > self.max_speed1) or abs(
                            total_time1 / self.nb_steps[-1][1]) < self.max_speed2:
                total_time = total_time2
            else:
                total_time = total_time1
            self.motor1.speed.append(abs(total_time / self.nb_steps[-1][0]))
            self.motor2.speed.append(abs(total_time / self.nb_steps[-1][1]))"""
    
        if not self.nb_steps[-1][0]:
            self.motor1.speed = 0
            self.motor2.speed = self.max_speed2
        elif not self.nb_steps[-1][1]:
            self.motor1.speed = self.max_speed1
            self.motor2.speed = 0
        else:
            total_time1 = abs(self.max_speed1 * self.nb_steps[-1][0])
            total_time2 = abs(self.max_speed2 * self.nb_steps[-1][1])
            if (total_time1 > total_time2 and abs(total_time2 / self.nb_steps[-1][0]) > self.max_speed1) or abs(
                            total_time1 / self.nb_steps[-1][1]) < self.max_speed2:
                total_time = total_time2
            else:
                total_time = total_time1
            self.motor1.speed = abs(total_time / self.nb_steps[-1][0])
            self.motor2.speed = abs(total_time / self.nb_steps[-1][1])


    def pinInit(self):
        """
        Initialise les pins de la raspberry pour contrôler le moteur
        :return: None
        """
        if not error:
            GPIO.setmode(GPIO.BOARD)
            GPIO.setwarnings(False)
            GPIO.setup(self.pwm_servo, GPIO.OUT)
            for i in range(4):
                GPIO.setup(self.bobines_motor1[i], GPIO.OUT)
                GPIO.setup(self.bobines_motor2[i], GPIO.OUT)
        else:
            print(error)

    def tryError(self):
        """
        Renvoie une errur le cas échéant
        :return:
        """
        pass

    def setMicroStep(self):
        micro_step = min(self.motor1.micro_step, self.motor2.micro_step)
        self.max_speed = self.max_speed / micro_step
        self.r_step /= self.motor1.micro_step
        self.theta_step /= self.motor2.micro_step

    def clearUp(self):
        B = Point(-7.5, 12)
        r = B.r - self.M.r
        theta = B.theta - self.M.theta
        self.motor1.nb_steps = int(r / self.r_step + 0.5)
        self.motor2.nb_steps = int(theta / self.theta_step + 0.5)
        self.motor2.speed = self.max_speed1
        self.motor1.speed = self.motor2.nb_steps * self.motor2.speed / self.motor1.nb_steps

    def sleep(self):
        self.motor1.sleep()
        self.motor2.sleep()

    def stop(self):
        """self.servoMotor.setServo("up")
        self.motor1.stop()
        self.motor2.stop()"""
        if not error: GPIO.cleanup()
        self.power = False


class Motor:
    """
    Classe permettant de controller les moteurs 
    pas-à-pas indépendamment l'un de l'autre
    """
    nb = 1

    def __init__(self, bobines=0, position=0, nb_steps=0, speed=10):
        self.speed = speed
        self.time = 0
        self.micro_step = 2
        self.number = Motor.nb
        self.bobines = bobines
        self.position = position
        self.init_position = 0
        self.nb_steps = nb_steps
        self.button_pin = (16, 18)
        self.stop_left = False
        self.stop_right = False
        self.direction = {"left": -1, "right": 1}
        self.PWM = self.initPWM()
        self.motor_alim = self.setMicroStep()

        self.bt = bt.Buttons(self.button_pin)
        self.bt.start()

        Motor.nb += 1

    def checkTime(self):
        if self.nb_steps:
            if time.time() - self.time >= self.speed:
                self.moveMotor()
                self.time = time.time()

    def initPWM(self):
        pwm = []
        for i in range(4):
            pwm.append(GPIO.PWM(self.bobines[i], 1500))
            pwm[i].start(0)
        return pwm

    def setMicroStep(self):
        next = None
        previous = None
        motor_alim = [[1, 0, 0, 0], [0, 0, 0, 1], [0, 1, 0, 0], [0, 0, 1, 0]]
        new_alim = []
        for i in range(4):
            for j in range(4):
                if motor_alim[i][j]: previous = j
                if motor_alim[(i + 1) % 4][j]: next = j
            for j in range(self.micro_step):
                new_alim.append([0, 0, 0, 0])
                new_alim[-1][previous] = 1 - j / self.micro_step
                new_alim[-1][next] = j / self.micro_step
        return new_alim

    def initializePosition(self, direction='left'):
        while not self.bt.pressed[0]:
            self.position += self.direction[direction]
            self.setPins()
            time.sleep(0.01 / self.micro_step)

    def moveMotor(self):
        if self.number == 1:
            self.stop_right = self.stop_left = False
            if self.bt.pressed[0] and self.nb_steps < 0:
                self.stop_left = True
                return 0
            if self.bt.pressed[1] and self.nb_steps > 0:
                self.stop_right = True
                return 0
        if self.nb_steps != 0:
            rotation = int(self.nb_steps / abs(self.nb_steps))
            self.nb_steps -= rotation
            self.position += rotation
            self.init_position += rotation
            self.setPins()

    def setPins(self):
        if not error:
            for i in range(4):
                self.PWM[i].ChangeDutyCycle(self.motor_alim[self.position % (4 * self.micro_step)][i] * 100)

    def sleep(self):
        print("motor{}: sleep".format(self.number))
        if not error:
            for i in range(4):
                self.PWM[i].ChangeDutyCycle(0)

    def stop(self):
        print("motor{}: stop".format(self.number))


class ServoMotor:
    def __init__(self, pin):
        self.positions = {'up': 5.5, 'down': 2}
        self.frequency = 50
        self.pin = pin
        self.power = True
        self.pwm = GPIO.PWM(self.pin, self.frequency)
        self.pwm.start(self.positions['up'])

    def setServo(self, position):
        self.pwm.ChangeDutyCycle(self.positions[position])


class ManualMotor(Motor):
    def __init__(self, bobines, position=0, nb_steps=0, speed=100):
        Motor.__init__(self)
        self.bobines = bobines
        self.position = position
        self.nb_steps = nb_steps
        self.speed = speed
        self.move = False
        self.direction = 1

    def run(self):
        while self.power:
            if self.move:
                time.sleep(self.speed / 1000)
                self.moveMotor()
            else:
                time.sleep(0.1)

    def moveMotor(self):
        self.position += self.direction


class Origin:
    def __init__(self):
        self.x_0 = -7.5
        self.y_0 = 7

    def coords(self):
        return self.x_0, self.y_0


class Point(Origin):
    def __init__(self, x, y, coordinate="cartesian"):
        Origin.__init__(self)
        if coordinate == "cartesian":
            self.x, self.y = x, y
            self.newPolarCoords()
        else:
            self.r = x
            self.theta = y
            self.newCartesianCoords()

    def newPolarCoords(self):
        self.r = math.sqrt((self.x - self.x_0) ** 2 + (self.y - self.y_0) ** 2)
        if self.y == self.y_0:
            self.theta = 0
        else:
            self.theta = (self.y - self.y_0) / abs(self.y - self.y_0) * math.acos((self.x - self.x_0) / self.r)

    def newCartesianCoords(self):
        self.x = self.r * math.cos(self.theta) + self.x_0
        self.y = self.r * math.sin(self.theta) + self.y_0


if __name__ == "__main__":
    init = MotorControl()
    init.start()
    init.convertPoints([(12, 3), (4, 5), "up", (3, 7), "up", "down"])

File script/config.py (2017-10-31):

#!/usr/bin/env/python3
# -*- coding: utf-8 -*-

##### Stepper Motors #####
r_step = 0.0203
theta_step = 0.0056
micro_step = 8
max_speed1 = 20  # speed max in ms
max_speed2 = 80  # speed max in ms
sleep_servo = 0.4
pwm_frequency = 1500
pen_origin = (0, 7)


##### Raspberry #####
rpi_ip = "10.3.141.1"
pwm_servo = 8
turn_on_led = 19
working_led = 21
button_pin = (16, 18)
bobines_motor1 = (29, 31, 33, 35)
bobines_motor2 = (7, 11, 13, 15)

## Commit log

2017-02-23 Ajout des pièces créées sur Solidworks : chariot, support camera-chariot, support stylo et l'assemblage des trois
    [assemblage.SLDASM, chariot.SLDPRT, support camera-chariot.SLDPRT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]
2017-02-24 Ajout des scripts principaux
2017-02-24 Photo page de garde + suppression scripts Your branch is up-to-date with 'origin/master'.
2017-03-08 Ajout des images reconnaissance
2017-03-09 Ajout d'images (circuits intégrés, repères...)
2017-03-12 Ajout leds témoins
2017-03-18 Ajouts mises en plans
    [assemblage.SLDASM, camera.SLDDRW, camera.SLDPRT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]
2017-03-19 modifs mineurs
    [camera.SLDDRW]
2017-03-19 Retour des mises en plan
2017-03-31 Modifications majeures: ajout Thread
2017-04-09 envoyer sudoku à la Rasberry Pi
2017-04-09 Modification connexion Raspberry Pi
2017-05-07 ajout interrupteurs de fin de course
2017-05-07 ajout prise photo raspberry
2017-05-14 correction write + position stylo
    [display.py, extraction.py, main.py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]
2017-09-09 test avec la Raspberry
